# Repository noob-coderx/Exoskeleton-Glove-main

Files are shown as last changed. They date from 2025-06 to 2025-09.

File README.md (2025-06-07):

Review Assignment Due Date (https://classroom.github.com/a/NJLWAR4a)



<!-- DON'T MODIFY ANYTHING ABOVE -->

<!-- Modify from here -->
# MIRAGE - Motion Integrated Real Time Articulated Glove Emulator
This document serves as a comprehensive guide for the project submission. 
## Project Overview
The project is a portable, wearable, exoskeleton glove. The glove, once worn, is able to detect the motions of the hand and simulate the motion on Unity on our Laptop. The exoskeleton glove is 3d printed, and each finger joint has a rotary encoder in it, which is used to figure out the amount of rotation. 
### Project Name: Exoskeleton glove for sensing precise hand movements
### Team Number: Mon-16
### Team Members:
- Nishant Bhave   (22B2144)
- Prajwal Nayak   (22B4246)
- Reeyansh Shah   (22B0412)
- Shikhar Moondra (22B0688)
- Siddick Khatri  (22B4241)

### Problem Statement and Solution:
The problem statement was to build a sensing exoskeleton glove to measure precise movements of fingers. The exoskeleton glove has to sense precise angular movement of each of the joints of the finger. It needs to transmit the captured data to a laptop which will recreate this movement using a 3D hand simulation. We were expected to deliver a functional exeskeleton glove which can be worn by a user and a 3D simulated model which tracks the user's hand movements using the exoskeleton glove. Some other expectations are as follows:
- Should be able to measure 1 degree angular movements of each finger joint
- Should be able to recreate the simluated movement within 1 second lag
- Should be battery operated for atleast half hour.

We solved this problem in the following ways:
- We made a exoskeleton glove (3D printed whose files are in the 3D_models subdirectory), which has spaces to attach rotatry encoders in them and they bend enough to get a precise measurement of the bending of the joints. The rotary encoders are basically potentiometers where the angle rotated is proportional to the angle rotated given that the angle lies in the range 0 to 2 pi. 
- The readings of the encoders are read by the raspberry pi pico w (which has an inbuilt Wifi module) as values from 0 to 65536 (16 bit). These values are sent to the Printed Circuit Board (whose schematic is given in the pcb subdirectory).
- The PCB mainly has 2 multiplexers and the Raspberry pi pico W mounted on it. It has header pins for taking in the values of the encoders. The multiplexers, based on the select pin values given by the Rpi, select which rotary encoders to read. The outputs of the multiplexers are connected to the ADC pins on the Rpi. The Rpi takes these readings and sends it to the laptop wirelessly using the UDP protocol. The Rpi code was written on Thonny which I have uploaded on the /src/Rpi_code folder.
- The values sent by Rpi are recieved by a python code running on the PC which then does some slight filtering/smoothening and forwards the value to the app (designed by unity).
- The app has a rigged hand model (which was designed on blender whose design is in the others folder). It also has the code for recieving values and converting it to angles and showing the intended fingers  bending. There are two sets of calibration post which the hand starts making accurate movements (code on /src/unity_codes).

We having worked on developing an exoskeleton glove, which involved circuit design, sensor integration, and mechanical assembly.We as a team learnt a lot of technical skills from this project : 3D Modelling, Raspberry pi coding on Thonny, using multiplexers, designing PCBs, using blender, and unity (C#), wiresless transmission of data using UDP protocol This experience significantly enhanced our skills in time management, teamwork, and collaboration. We faced several challenges, particularly during PCB fabrication, which taught us the importance of early planning and maintaining buffer time to manage unforeseen delays. Working late into the night became common as we strived to meet deadlines while maintaining accuracy. We learned to divide tasks effectively, communicate clearly, and support each other through technical and logistical hurdles. A key takeaway was the ability to balance seeking guidance when necessary with independently troubleshooting problems. Overall, it was a comprehensive learning experience that combined technical rigor with essential project management and interpersonal skills.

Due to time constraints and some last minute issues of raspberry pi heating up, we were not able to power the exoskeleton glove with the battery and decided to power it using our PC instead. Nevertheless the transmission is still over wifi setup using our hotspot. We look forward to debug this issue rigorously and make the glove operational using a battery for portable deployability. The Glove has immense application in rehabilitation and VR gaming industry and although we attempt to show its functioning though the prosthetic arm, we are excited to implement this project on a standard pneumatic actuated glove to help out and do our bit for the society!

## 1. Source Code

All source code files are organized under the `/src` directory. Each subdirectory has clear descriptions about their purpose and functionality. Every subfolder has a README.MD file which explains the purpose of the code and all the commands used.

### Folder Structure:
```plaintext
/Project-Root 
├── /src 
  ├── /Rpi_code
     ├── rpi.py
  ├── /python-code
     ├── python.py
  ├── /unity_codes
     ├── /handcontroller
        ├── /Hand_control.cs
     ├── /camera_rotation
        ├── /CameraOrbit.cs
```

## 2. PCB Design

The project involves designing a printed circuit board (PCB). We have provided the design files in the `/pcb` folder. The PCB was designed using KiCAD. The picture of our final PCB Layout is present under the `/pcb/<PCB_X>/pictures` folder.

### Folder Structure:
```plaintext
/Project-Root 
├── /pcb 
  ├── /PCB1
    ├──/pictures
      ├──3D view.png
      ├──PCB layout.png
      ├──circuit.png
    ├── PCB.kicad_pcb 
    ├── pcb.kicad_sch
```
---

## 3. 3D Models
The project includes 3D models that require 3D printing. The files are placed in the `/3d_models` directory. Create separate subfolders for different models and provide a description of the design process and tools used.

### Folder Structure:
```plaintext
/Project-Root
├── /3d_models
  ├── /Exoskeleton Glove
     ├── Rot Pot V1.jpg
     ├── Rot Pot v1.stl
     ├── connect 1.jpg
     ├── connect 1.stl
     ├── connect 2.stl
     ├── connect base.jpg
     ├── connect base.stl
     ├── connect2.jpg
     ├── index sensor place 1 velcro v12.jpg
     ├── index sensor place 1 velcro v12.stl
     ├── palm base v1.jpg
     ├── palm base v1.stl
     ├── pcb case easy v1.jpg
     ├── pcb case easy v1.stl
     ├── pcb case top v1.jpg
     ├── pcb case top v1.stl
     ├── sensor body attachment back v13.jpg
     ├── sensor body attachment back v13.stl
     ├── sensor body attachment base v10.jpg
     ├── sensor body attachment base v10.stl
     ├── sensor body attachment v14.jpg
     └── sensor body attachment v14.stl
  ├── /Prosthetic Arm
     ├── Arm_Cover.jpg
     ├── Arm_Cover.stl
     ├── Assemble_Prosthetic_Arm.png
     ├── Finger_Index.jpg
     ├── Finger_Index.stl
     ├── Finger_Middle.jpg
     ├── Finger_Middle.stl
     ├── Finger_Pinky.jpg
     ├── Finger_Pinky.stl
     ├── Finger_Ring.jpg
     ├── Finger_Ring.stl
     ├── Finger_Thumb.jpg
     ├── Finger_Thumb.stl
     ├── Right_Hand.jpg
     ├── Right_Hand.stl
     ├── arm servo placement v1.jpg
     └── arm servo placement v1.stl

```
---

## 4. Bill of Materials (BOM)

A complete Bill of Materials (BOM) listing of all the hardware components used in the project is provided in this file including both parts obtained from the lab and parts ordered from external vendors or purchased locally.

### Folder Structure:
```plaintext
/Project-Root 
├── bom.xlsx
```
---

## 5. Reports and Presentations

The project presentation and reports include a brief overview of your project, objectives, design process, results, and conclusions. This should include all the milestone submission presentations.

### Folder Structure:
```plaintext
/Project-Root
  ├── /reports 
    ├── Milestone 0 P-12 MON-16.pdf
    ├── Milestone 1 P-12 MON-16.pdf
    ├── Milestone 2 P-12 MON-16.pdf
    ├── Milestone 3 P-12 MON-16.pdf
    ├── Milestone 4 P-12 MON-16.pdf
```

## 6. Other Documents
This directory consists of the Circuit digrams used, making video and the final prototype images of our poject.
### Folder Structure:
```plaintext
/Others
  ├── Circuit Diagram Prosthetic Arm.pdf.jpg
  ├── Circuit_Diagram_Exoskeleton_Glove.pdf
  ├── Making Video.mp4
  ├── Prototype Exoskeleton Glove.jpg
  ├── Prototype Prosthetic Arm.png
  └── Wiring image of Exoskeleton Glove.jpg
```

---

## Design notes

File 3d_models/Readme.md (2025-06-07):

### This directory contains the folders for the 3D Models of our Exoskeleton Glove as well as the prosthetic arm prototype
1. Exoskeleton Glove
2. Prosthetic Arm

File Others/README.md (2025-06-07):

This directory contains the final circuit diagrams of our prototype of both Exoskeleton Glove and the Prosthetic Arm, also with the images of wiring in the circuit, and the final version of our prototype. 
It also contains the User Manual which describes on how to do the Mechanical Assembly and explains the circuit connections and caliberation Modes.

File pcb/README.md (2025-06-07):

This is the folder for our PCB design. We had a single PCB.

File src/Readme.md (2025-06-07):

This is the src folder which has the codes for the raspberry pi, untiy and python code for data reception.
1. **Raspberry Pi Pico W code and ESP32 Code** in the subdirectory microcontroller.
2. **Running Unity and Running codes** in the subdirectory unity_codes.
3. **Code for using python for reception of data wirelessly** in the subdirectory python-code

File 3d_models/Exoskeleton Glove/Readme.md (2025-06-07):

### This directory contains the STL files for fabiracation (3D Printing) of the Exoskeleton Glove.
All parts have been manufactured at 50% infill density for higher strength due to delicate parts. It is advised to use normal supports with brim (outer only) so that all parts get manufactured accurately, especially the smaller complex parts

1. Connect 1, Connect 2 connect base at attached using a hinge to propogate the joint angles accurately to the rotary potentiometer.
2. Index Sensor place 1 velcro v12 features a slide locking mechanism for the rotary encoder avoiding press-fit mechanism due recurrent failure and breakage. We have assembled the sensing glove using velcro to make it compatible for any arm size.
3. sensor body attachment v14, sensor body attachment base, sensor body attachment back, and palm base constitute the components fixed on the back side of the palm. The assembly of sensor body attachment v14, sensor body attachment base, sensor body attachment back helps achieve a 2 DOF sensing of motion in the lateral and transverse plane.
4. pcb case easy v1 and pcb case top v1 are rhe enclosures for PCB with slots for wires

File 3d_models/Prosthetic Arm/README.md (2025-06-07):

### This directory contains the STL files for fabiracation (3D Printing) of the Prosthetic Arm.
[Reference](https://www.viralsciencecreativity.com/post/arduino-flex-sensor-controlled-robot-hand)

We 3D printed all the parts with 10% infill density.
All the printed parts were assembled using elastic strings and cords as shown in the final prototype.  
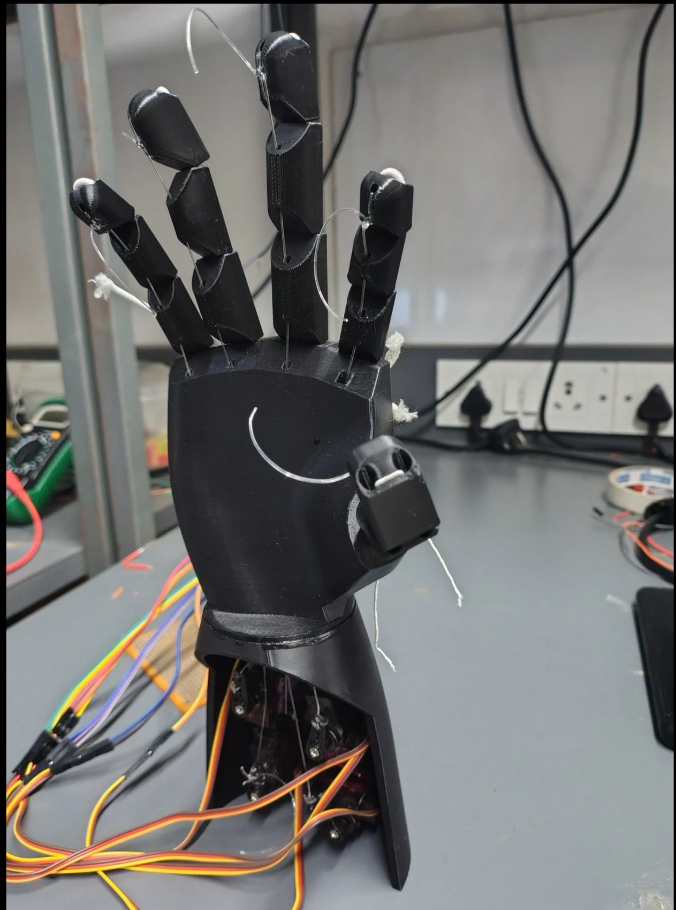
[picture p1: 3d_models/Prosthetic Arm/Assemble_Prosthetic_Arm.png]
Prosthetic Arm


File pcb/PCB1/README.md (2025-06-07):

In a nutshell, our design collects data from rotary potentiometers serially, sends them to Rpi pico which in turn quickly cycles through the available channels in a round robin fashion while powering everything using an LM2596 Buck converter

Our PCB design has the ability to support upto 24 rotary potentiometers due to which we have 24 ports connected to ground and 24 ports connected to VCC(3.3V output from sensor). We connected these to the 3.3v supply of Pico instead of our main power supply which is LM2596 because cd74hc4067 multiplexers are designed to take an input between 0 and 3.3V.
External power is inputted at the 2x1 connector which is also the input of out LM2596 buck converter, the output of this converter powers both our cd74hc multiplexers. Raspberry pico runs a program in which it outputs different values periodically at 4 different GPIO pins(2,3,4,5) which are connected to s0,s1,s2,s3 of multiplexer 1 and GPIO pins(18,19,20,21) which are connected to s0,s1,s2,s3 of multiplexer 2. The output of each of the multiplexers(sig) is connected to 2 out of 3 ADC pins in rpi pico(GPIO 26,27,28). This output is transmitted to unity and esp32 which controls the prosthetic arm

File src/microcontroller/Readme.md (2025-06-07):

# Raspberry Pi Pico W ADC MUX Communication

This project uses a **Raspberry Pi Pico W** to:
- Connect to a Wi-Fi network.
- Read analog values from two 16-channel multiplexers (MUX).
- Send these values over UDP to a laptop in real time.

The source code reads from either MUX1 or MUX2 using GPIO and ADC pins. It selects channels using S0-S3 pins and reads the analog voltage using onboard ADCs. It transmits each channel's analog reading over a UDP socket to a specified IP and port.

---

## Microcontroller Model

**Raspberry Pi Pico W**

---

## IDE Used

**Thonny IDE** (Recommended for MicroPython development)

---

## Upload and Run Instructions

### Prerequisites

1. Install **Thonny IDE** from: https://thonny.org  
2. Ensure **MicroPython firmware** is installed on your Raspberry Pi Pico W.
3. Connect your Pico W via USB.

###  Uploading the Code

1. Open Thonny.
2. Set the interpreter:  
   `Tools > Options > Interpreter > MicroPython (Raspberry Pi Pico)`
3. Paste the script into Thonny.
4. Replace:
   - `SSID` with your Wi-Fi network name.
   - `PASSWORD` with your Wi-Fi password.
   - `LAPTOP_IP` with your laptop’s IP address.
5. Click **Run (▶️)** to execute the script on the Pico W.

##  Notes

- The Pico W will print its IP address once connected to Wi-Fi.
- It loops over analog channels and transmits the value over UDP port `5005`.
- To receive data on the laptop, you can use a UDP socket script in Python or software like netcat.

---

Modifications:
- Configured GPIO and ADC pins for 2 MUX units.
- Implemented UDP communication for real-time analog data transfer.
- Optimized loop with delay for stable channel switching.

# ESP32-Based Servo Motor Control via UDP

This project enables real-time control of servo motors using joint angle data received over UDP. An ESP32 board connects to Wi-Fi and receives lower joint angles from a laptop. These angles are used to drive corresponding servo motors via a PCA9685 driver, enabling gesture replication or robotic hand motion.

## Features

- Wi-Fi-based UDP communication
- Real-time servo actuation
- Automatic joint calibration
- Rolling average filtering for noise reduction
- Smooth motor transitions to prevent jerks

## Hardware Required

- ESP32 Development Board  
- PCA9685 PWM Driver  
- Servo Motors  
- External 5V Power Supply  
- Connecting wires

## Communication Protocol

- **Format:** `<joint_number> <angle_value>` (e.g., `1 120`)  
- **Port:** 8888 (UDP)  
- **Sender:** Laptop or external device

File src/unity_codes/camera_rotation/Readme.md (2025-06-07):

This script enables the camera in a Unity scene to orbit around a target object based on mouse input. It calculates an offset and updates the camera's position and rotation every frame, providing intuitive camera control for 3D object inspection or gameplay scenes.

Upload & Run Instructions
Microcontroller Model: Not applicable – this script runs in the Unity Engine on a PC or supported platform.

IDE Used: Unity Editor (e.g., Unity 2021.3 or later)

Steps to Compile and Upload:
Open Unity Hub and create a new 3D project or open an existing one.

Add the Script:

Create a new C# script in the Assets folder named CameraOrbit.cs.

Copy and paste the script code into this file.

Assign the Script:

Attach the CameraOrbit script to your main camera in the Hierarchy.

Drag the target GameObject (the object to orbit around) into the script’s target field in the Inspector.

Run the Scene:

Click the Play button in Unity to test the camera orbit functionality.

Example Command (in Unity Console, for debug purposes):
csharp
Copy code
Debug.Log("Camera Orbit script is active");
Let me know if you want a second entry for Microcontroller2, or if you’re using this Unity camera in a larger system with real hardware!

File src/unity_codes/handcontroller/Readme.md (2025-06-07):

   - **Folder Name**: Name it according to the microcontroller, e.g., `Microcontroller1`, `Microcontroller2`.
   - **Description**: A brief description of what each microcontroller’s source code does and its role in the project in a README.md file.
   - etailed instructions on how to upload and run the code on the microcontroller. This should include:
  - The microcontroller model (e.g. STM32, RPi Pico).
  - The Integrated Development Environment (IDE) used for programming (e.g., STM32CubeIDE, VSCode, Thonny IDE).
  - Steps for compiling and uploading the code to the device.
  - Example command to upload (if applicable).
  - 3. **Code Comments**:
- Every source file should be properly commented to describe the purpose and function of each section of code.
- If you have made modifications to an existing code template or framework, comment clearly with your team name and indicate what changes were made.

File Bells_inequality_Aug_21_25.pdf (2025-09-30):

# EPR, Bell’s Inequality, and the E91 Protocol

## Gaurav S. Kasbekar Dept. of Electrical Engineering IIT Bombay

# References

## - C. Bernhardt: Chapter 5 - M. Nielsen and I. Chuang: Section 2.6

# Copenhagen Interpretation

- Named after city where Neils Bohr lived
- According to Copenhagen interpretation:
❑ Before a measurement is made, a quantum system exists in a superposition of multiple states
- e.g., particle might be considered to be in multiple locations simultaneously
❑ The act of measuring forces the system to "collapse" into a single, definite state
- Specific state it collapses into is probabilistic, i.e., it is governed by probabilities, not determined with certainty
❑ Observer or measuring apparatus plays crucial role in determining outcome of quantum event
- Observer not merely passively observing, but actively influencing system's state
- Some physicists, e.g., Einstein and Schrodinger did not subscribe to this model, in particular, to:
❑ interpretation of states jumping with given probabilities to basis states, and
❑ concept of action at a distance in entanglement
- They thought there should be a better model using:
❑ hidden variables and local realism (details later)
- John Stewart Bell devised an ingenious test, which could distinguish between above two models
- Later, several experiments based on Bell’s result were conducted, which showed that: ❑ Einstein and Schrodinger’s view was wrong and Copenhagen interpretation is correct

# Local Realism

- A concept in physics that combines two ideas: ❑locality
❑realism
- Locality:
❑an object's properties are determined only by its immediate environment
❑any influence on that object can only travel at or below speed of light ❑distant objects cannot instantaneously affect each other
- Realism:
❑objects have definite, pre-existing properties, regardless of whether they are being observed or measured
- Einstein, Boris Podolsky, and Nathan Rosen (EPR) published a paper, which stated that:
❑special theory of relativity implied that information could not travel faster than speed of light,
❑but instantaneous action at a distance (as in entangled particles) would mean that information could be sent from Alice to Bob instantaneously
- This problem known as EPR paradox

# Hidden Variables

## - Hidden variables:

### ❑properties of particles, to which we do not have access, which determine the outcomes of quantum measurements even before the measurements are actually made

## - EPR proposed that:

### ❑quantum mechanics might be incomplete because

it does not account for these hidden variables,

### ❑quantum mechanics only provides probabilistic predictions, while a more complete theory (including hidden variables) could offer deterministic outcomes

# Versions of Bell’s Inequality

## - There are several versions of Bell’s inequality - We discuss two versions

# Bell’s Inequality: Version 1 Clauser, Horne, Shimony, and Holt (CHSH Inequality)

# CHSH Inequality

- Imagine we perform following experiment, illustrated in Fig.
- Charlie prepares two particles:
❑ sends one particle to Alice, and second particle to Bob
- Once Alice receives her particle, she performs a measurement on it
- She has available two different measurement apparatuses, so she could choose to do one of two different measurements
- These measurements are of physical properties which we shall label:
❑ PQ and PR, respectively
- Alice doesn’t know in advance which measurement she will choose to perform:
❑ when she receives particle, she randomly decides which measurement to perform
- For simplicity, assume that the measurements can each have one of two outcomes, + 1 or −1
- Suppose Alice’s particle has a value:
❑ Q for the property PQ
❑ R for the property PR

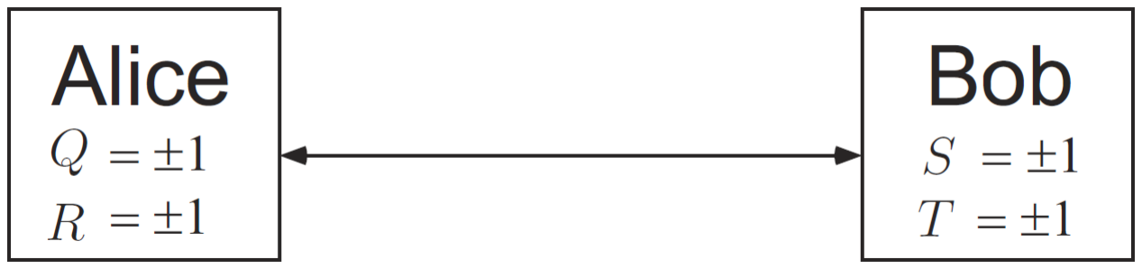
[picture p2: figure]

Ref: M. Nielsen and I. Chuang, “Quantum Computation and
Quantum Information”

# CHSH Inequality (contd.)

## - Similarly, Bob is capable of measuring one of two

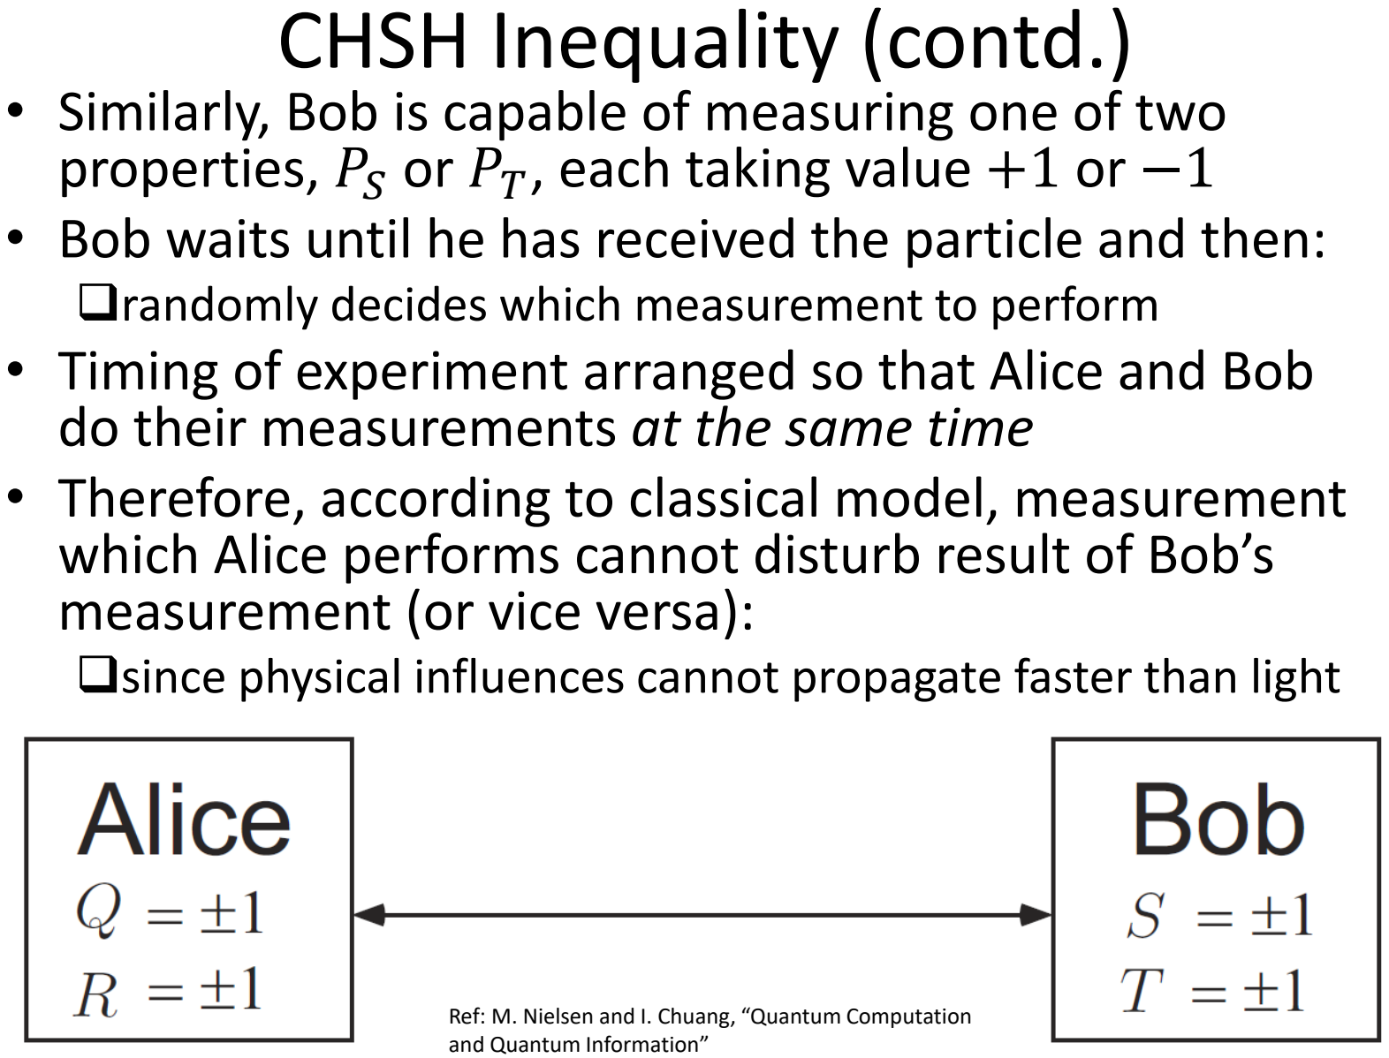
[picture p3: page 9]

## properties, PS or PT, each taking value +1 or −1 - Bob waits until he has received the particle and then:

### ❑randomly decides which measurement to perform

## - Timing of experiment arranged so that Alice and Bob do their measurements at the same time - Therefore, according to classical model, measurement which Alice performs cannot disturb result of Bob’s measurement (or vice versa):

### ❑since physical influences cannot propagate faster than light

Ref: M. Nielsen and I. Chuang, “Quantum Computation and Quantum Information”

# CHSH Inequality (contd.)

- Note that:
1) QS + RS + RT − QT = Q + R S + R − Q T
- Since R,Q ∈ {−1, +1}, it follows that:
❑ Q + R S = 0 or R − Q T = 0
- In either case, from 1), we get that:
2) QS + RS + RT − QT = ±2
- Let p(q, r, s,t) be probability that, before the measurements are performed, system is in state where Q = q, R = r, S = s, T = t
❑ these probabilities may depend on how Charlie performs his preparation, and on experimental noise
- By 2), we get:
3) E QS + E RS + E RT − E QT = σq,r,s,t p(q, r, s,t) (
)

qs + rs + rt −
qt ≤ 2
- Inequality in 3) known as CHSH inequality
- Note that we derived 3) using classical model (assumption of realism)

Ref: M. Nielsen and I. Chuang, “Quantum Computation and Quantum Information”

# CHSH Inequality (contd.)

## - Recall: CHSH inequality:

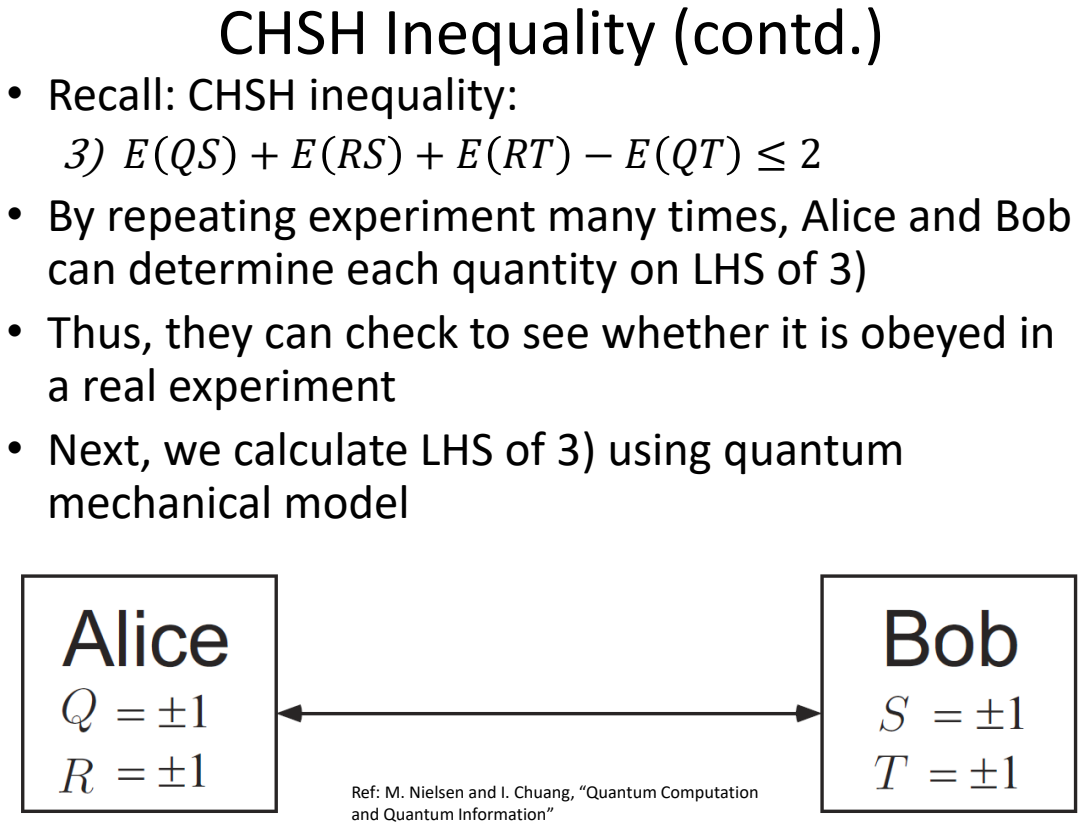
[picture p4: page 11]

• By repeating experiment many times, Alice and Bob
can determine each quantity on LHS of 3)
• Thus, they can check to see whether it is obeyed in
a real experiment
• Next, we calculate LHS of 3) using quantum
mechanical model

Ref: M. Nielsen and I. Chuang, “Quantum Computation
and Quantum Information”

# CHSH Inequality (contd.)

- Recall: CHSH inequality:
3) E QS + E RS + E RT − E QT ≤ 2
- Suppose Charlie prepares a quantum system of two qubits in state:
❑ |ψۧ =

|01ۧ−|10ۧ
2
- He passes:
❑ first qubit to Alice, and
❑ second qubit to Bob
- They perform measurements of following observables:
❑ Q = Z1, S =

−Z2−X2
2
❑ R = X1, T =

Z2−X2
2
❑ (Note: subscript 1 (respectively, 2) denotes qubit of Alice (respectively, Bob))
- Exercise: Show that eigenvalues of each of the above observables Q, R, S, and T are ±1
❑ recall: eigenvalues of observables are measurement outcomes; hence, the possible outcomes are ±1 for each observable
- Exercise: Show that average values of above observables are:
❑ QS =

1
2

; RS =

1
2

; RT =

1
2

; QT = −

1
2
❑ (use the fact that M ≡ ۦ | | ۧ(
- Thus:
4) QS + RS + RT − QT = 2 2
- Note that 3) and 4), which were obtained using classical and quantum mechanical model, respectively, contradict each other

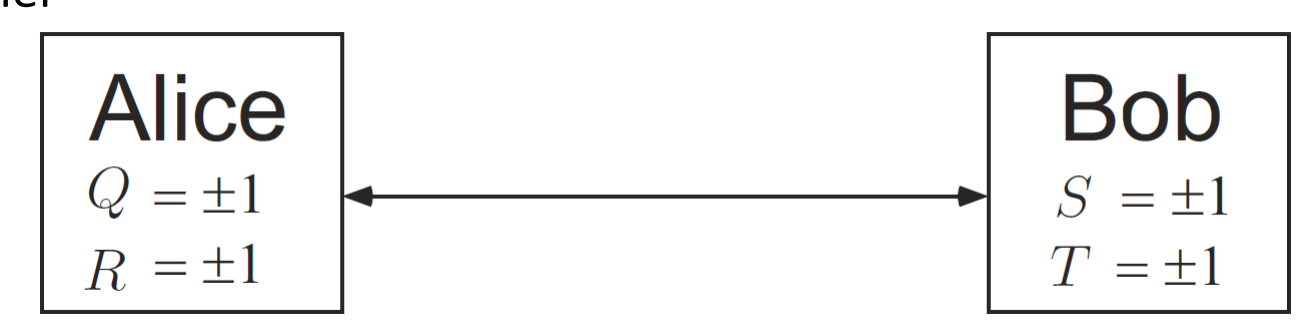
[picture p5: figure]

Ref: M. Nielsen and I. Chuang, “Quantum Computation and
Quantum Information”

# CHSH Inequality (contd.)

- Recall:
❑|ψۧ =

|01ۧ−|10ۧ
2
❑Q = Z1, S =

−Z2−X2
2
❑R = X1, T =

Z2−X2
2
- We now outline the proof of QS =

1
, which is part of above

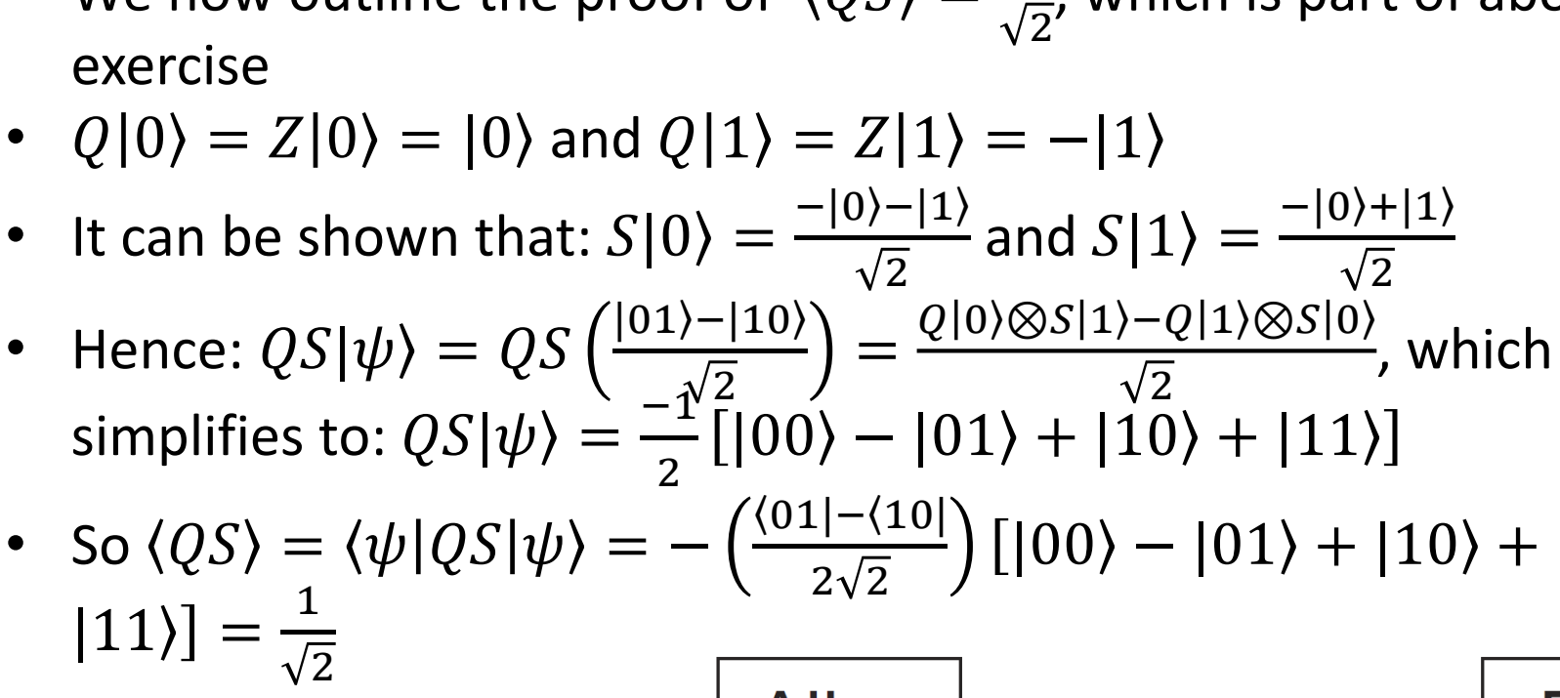
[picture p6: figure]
exercise; 0ۧ = |0ۧ and Q; • It can be shown that: S|0ۧ =; and S|1ۧ =; • Hence: QS|ψۧ = QS |01ۧ−|10ۧ; , which; simplifies to: QS|ψۧ =

Ref: M. Nielsen and I. Chuang, “Quantum Computation and
Quantum Information”

# CHSH Inequality (contd.)

- Recall:
❑ |ψۧ =

|01ۧ−|10ۧ
2
❑ Q = Z1, S =

−Z2−X2
2
❑ R = X1, T =

Z2−X2
2
- Note that we need to calculate E QS , which is the average value of the product of two scalars
- But we equated it to QS = ۦ | Q | ۧ = ۦ | ⊗ | ۧ
- Why does the tensor product Q ⊗ S correspond to the measurement outcome qs, which is a product of two scalars?
- Recall the spectral decompositions:
❑ Q = σq qPq and
❑ S = σs sPs
❑ where Pq is projector onto eigenspace of Q with eigenvalue q
- So:
❑ Q ⊗ S = σq qPq ⊗ σs sPs = σq,s qs Pq ⊗ Ps
- Hence, Q ⊗ S is an observable with corresponding measurement outcomes qs

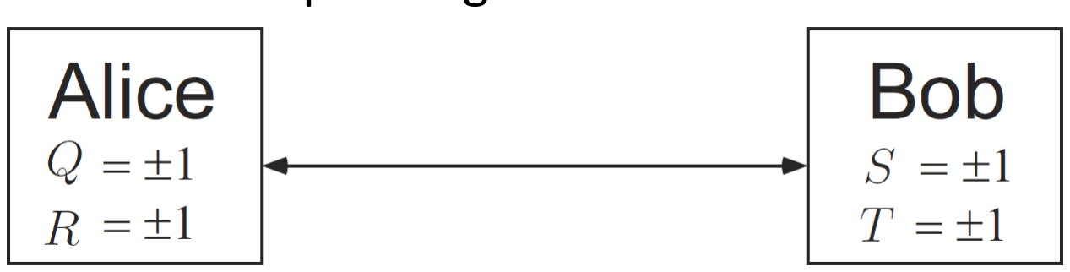
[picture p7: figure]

Ref: M. Nielsen and I. Chuang, “Quantum Computation and
Quantum Information”

# CHSH Inequality (contd.)

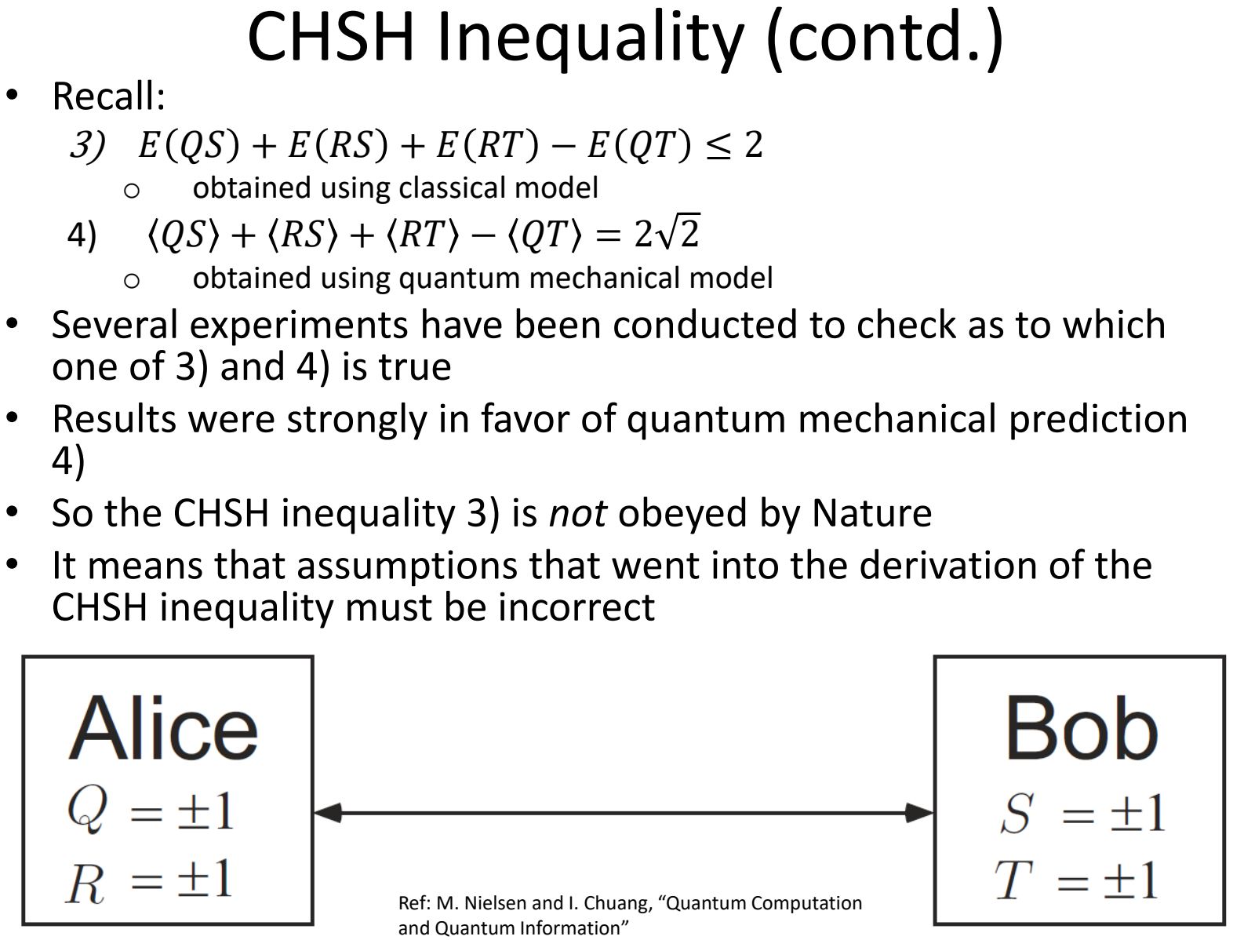
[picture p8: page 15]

- Recall:
3) E QS + E RS + E RT − E QT ≤ 2
- obtained using classical model
4) QS + RS + RT − QT = 2 2
- obtained using quantum mechanical model
- Several experiments have been conducted to check as to which one of 3) and 4) is true
- Results were strongly in favor of quantum mechanical prediction 4)
- So the CHSH inequality 3) is not obeyed by Nature
- It means that assumptions that went into the derivation of the CHSH inequality must be incorrect

Ref: M. Nielsen and I. Chuang, “Quantum Computation and Quantum Information”

# CHSH Inequality (contd.)

- Recall:
3) E QS + E RS + E RT − E QT ≤ 2
- obtained using classical model
4) QS + RS + RT − QT = 2 2
- obtained using quantum mechanical model
- There are two assumptions made in various proofs of 3) which are questionable: realism and locality ❑ Realism:
❑ assumption that the physical properties PQ, PR, PS

, and PT have definite values, Q, R, S, and T, which exist independent of observation
❑ We used this in above derivation to write E QS + E RS + E RT − E QT = σq,r,s,t p(q, r, s,t) qs + rs + rt − qt , where p(q, r, s,t) is probability that before the measurements are performed, system is in state where Q = q, R = r, S = s, T = t
❑ Note: If we try to define p(q, r, s,t) to be probability that after measurements are performed, the outcomes will be Q = q, R = r, S = s, T = t, then such a joint distribution does not exist in general since either PQ or PR (respectively, PS or PT) is measured, but not both
❑ Locality:
❑ assumption that Alice performing her measurement does not influence the result of Bob’s measurement
❑ If this assumption holds, then we can write:
❑ E QS = E Q)E(S , E RS = E R)E(S , E RT = E R)E(T , and E QT = E Q)E(T
❑ So E QS + E RS + E RT − E QT = E S E Q + E R + E T E R − E Q ≤ | E Q + E R | + | E Q − E R | ≤
2 max |E Q)|, |E(R | ≤ 2
- These two assumptions together constitute assumption of local realism:
❑ must be dropped

Ref: M. Nielsen and I. Chuang, “Quantum Computation and Quantum Information”

# Bell’s Inequality: Version 2

# Entangled Qubits in Different Bases

- Consider two entangled qubits in state:

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
- Now, consider a new orthonormal basis |b ۧ 0 , |b ۧ 1 : ❑where the components of |b ۧ 0 and |b ۧ1 are real numbers
- Claim:

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
|b ۧ 0 ⊗ |b ۧ 0 +

1
2

|b ۧ 1 ⊗ |b ۧ 1
- Proof:
❑Let |b ۧ 0 =

a
b

and |b ۧ 1 =

c
d

, where a, b, c, d ∈ R
❑Then 1
0

= a

a
b

+ c

c
d
1) So 1
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
2) Similarly, 0
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
❑Adding 1) and 2), we get: 1 0

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
= |b ۧ 0 ⊗ |b ۧ 0 + |b ۧ 1 ⊗ |b ۧ1

## Bases Used for Bell’s Inequality

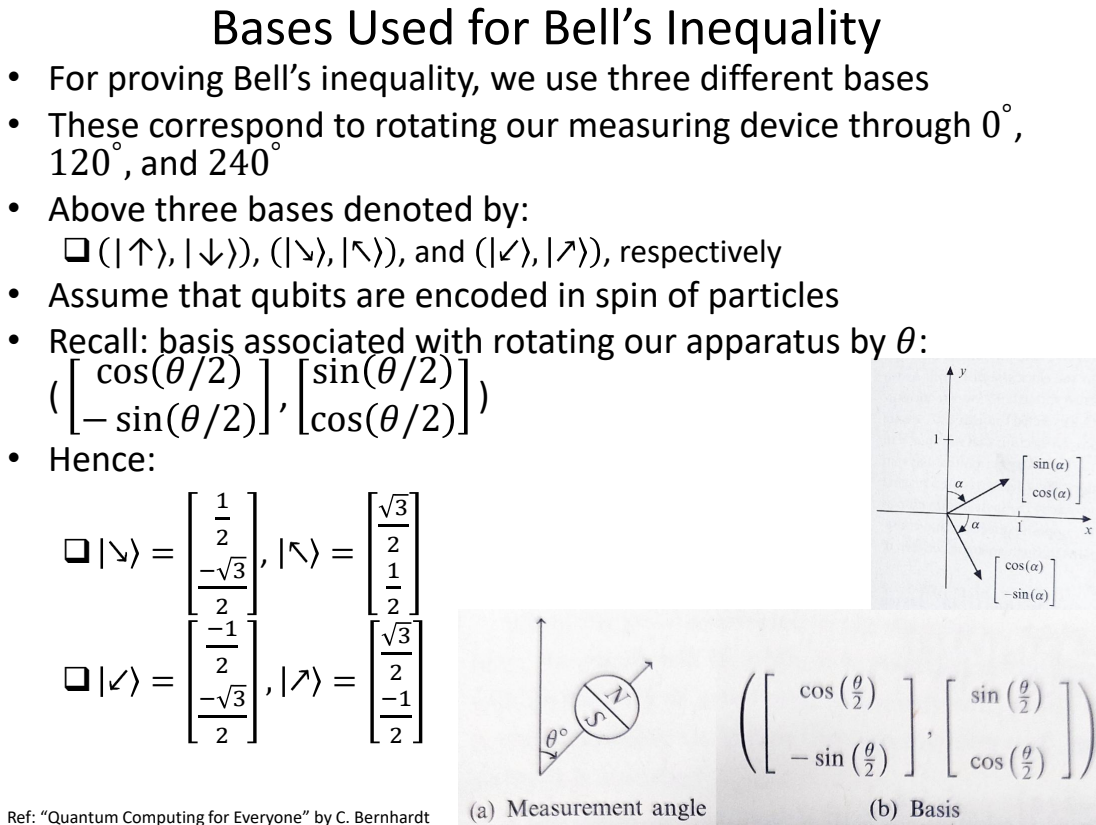
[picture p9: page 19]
, and 240; , and; , respectively; sin θ/2 cos θ/2

• For proving Bell’s inequality, we use three different bases
• These correspond to rotating our measuring device through 0
• Above three bases denoted by:
• Assume that qubits are encoded in spin of particles
• Recall: basis associated with rotating our apparatus by θ:
cos θ/2
− sin θ/2
• Hence:

Ref: “Quantum Computing for Everyone” by C. Bernhardt

# Classical Explanation of Entanglement

### - Consider two entangled qubits:

❑one with Alice and other with Bob
❑state of the qubits is 1
2

|↑ۧ|↑ۧ +

1
2

|↓ۧ|↓ۧ

### - Recall:

❑when Alice and Bob perform a measurement of their qubits in basis |↑ۧ, |↓ۧ , both get same answer (either 0 or 1)

### - Recall: for proving Bell’s inequality:

❑we rotate our measuring device through 0

°
, 120

°
, and 240

°
❑we measure spin of particles in the bases |↑ۧ, |↓ۧ , | , | ,
and | ,

### - Classical theory states:

❑there is a definite outcome of the measurement in each basis that is already determined before we perform the measurement (realism)

### - Quantum theory states:

❑outcome of measurement not determined until the time we perform the measurement

# Bell’s Inequality

- We generate a stream of n pairs of qubits:
❑ from each pair, one sent to Alice and other to Bob
- Each pair of qubits is in state:

❑

1
2

|↑ۧ|↑ۧ +

1
2

|↓ۧ|↓ۧ
- Alice:
❑ measures each qubit in direction 0

°
, 120

°
, or 240

°
- for each qubit, direction of measurement selected uniformly at random, independently of other qubits
❑ does not keep track of direction she chose for a qubit
❑ records the outcome (0 or 1) of each measurement
- Subsequently, Bob does the same for his qubits:
❑ his directions of measurements selected independently of Alice
- In this way, Alice and Bob generate strings of length n each of 0s and 1s
- What is the fraction of bits of these strings in which Alice and Bob are in agreement?
- Bell realized that quantum mechanics model and classical model gave different numbers for the answer

## Answer of Quantum Mechanics

- Consider a pair of qubits, which is in state:

❑

1
2

|↑ۧ|↑ۧ +

1
2

|↓ۧ|↓ۧ
- Recall: if Alice and Bob select same direction of measurement (i.e., same basis), their outcomes are same
- Consider case where they select different directions of measurement
- E.g.: suppose:
❑ | Alice chooses | ,
❑ | Bob chooses | ,
- Entangled state can be written as:

❑

1
2

+

1
2
- When Alice performs measurement:
❑ | she gets 0 and state jumps to | w.p.

1
2
❑ | she gets 1 and state jumps to | w.p.

1
2
- Suppose Alice gets 0 and state jumps to
- Now:
❑ | =
| 1
| 2 +
| 3
| 2
- So when Bob performs measurement:
❑ | gets 0 w.p.
| 1
| 4 and 1 w.p. | 3
| | 4
- Thus, when Alice gets 0, states of Alice and Bob agree w.p.
| | | | | 1
| | | | | 4
- Exercise: Show that even when Alice gets 1, states of Alice and Bob agree w.p.

1
4
- In summary:
❑ | when Alice chooses | , | and Bob chooses | , | , their bits agree w.p.

1
4

and disagree w.p.

3
4
- Exercise: Show that in all other cases in which Alice and Bob choose different bases, their bits agree w.p.

1
4

and disagree w.p.

3
4
- In summary, for a given pair of qubits:
❑ | w.p.
| 1
| 3

, Alice and Bob choose same basis and their bits agree w.p. 1
❑ | w.p.
| 2
| 3

, Alice and Bob choose different bases and their bits agree w.p.

| | | | | 1
| | | | | 4
- According to quantum mechanics model, what is the fraction of bits of the strings of Alice and Bob for which the bits are in agreement?
❑ | 1
| 2

- | Classical view: | Classical Answer

❑ Measurements in all directions determined right from the start
- There are eight possible configurations:
❑ 000, 001, 010, 011, 100, 101, 110, 111
❑ where the three bits in each configuration give the answer (0 or 1) if we measure a qubit in bases |↑ۧ, |↓ۧ , | , | ,
and | , | , respectively
- Due to the entanglement between qubits of Alice and Bob:
❑ for each pair of qubits, configurations of Alice and Bob are identical
- Table shows all possible outcomes of measurement, where:
❑ a, b, and c denote |↑ۧ, |↓ۧ , | , | , and | , | , respectively
❑ | x, y , where x, y ∈ {a, b, c}, denotes that Alice (respectively, Bob) measures qubit in basis x (respectively, y)
❑ Entries in table show whether measurements agree (A) or disagree (D)
- Probabilities that should be assigned to different configurations unknown
- Since Alice and Bob choose each of their three bases with equal probabilities, each of the nine pairs of bases occurs w.p.

1
9

Ref: “Quantum Computing for Everyone” by C. Bernhardt

- Note that each row contains at least five As
- Hence, overall probability that measurements of Alice and Bob result in same outcome is at least ⁵
9
- According to classical model, what is the fraction of bits of the strings of Alice and Bob for which the bits are in agreement?
❑at least ⁵
9

# Summary of Bell’s Result

## - Recall above question:

### ❑What is the fraction of bits of the strings in which Alice and Bob are in agreement?

## - Answer of quantum mechanics: ¹

2

## - Classical answer: at least ⁵

9

## - Thus, Bell’s test gives us a way to distinguish between the two theories - Above experiment has been performed by several researchers - Outcomes have always been in agreement with quantum mechanics

# E91 QKD Protocol

- In 1991, Artur Ekert proposed QKD protocol based on entangled qubits used in Bell’s test
- We generate a stream of 3n pairs of qubits:
❑ from each pair, one sent to Alice and other to Bob
- Each pair of qubits is in state:

❑

1
2

|↑ۧ|↑ۧ +

1
2

|↓ۧ|↓ۧ
- Alice and Bob measure each qubit using a random choice of three bases: ❑ as in Bell test
- As in BB84 protocol, for each measurement:
❑ Alice and Bob record both outcome and basis that they chose
- After Alice and Bob have made 3n measurements:

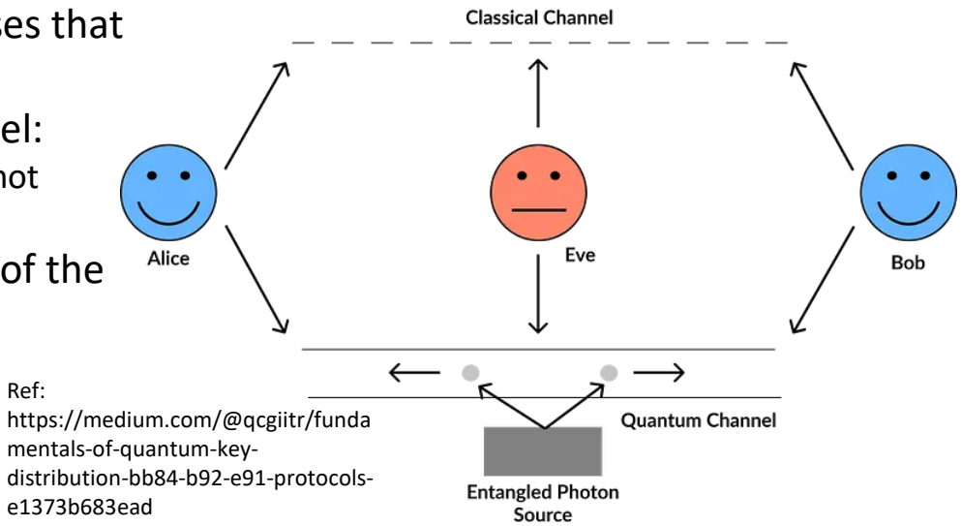
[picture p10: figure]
https://medium.com/@qcgiitr/funda mentals-of-quantum-key- distribution-bb84-b92-e91-protocols- e1373b683ead

Ref:

❑They compare the sequences of bases that
they chose
❑This can be done on insecure channel:
oNote that they only reveal bases, but not measurement outcomes
❑They will agree on approximately n of the sequence of bases

# E91 QKD Protocol (contd.)

- For the n pairs of qubits for which Alice and Bob selected same basis:
❑ Alice and Bob get same measurement outcome (0 or 1)
- This string of n bits will be their key if an eavesdropper Eve is not listening in
- Now Alice and Bob test to find if Eve is present
- If Eve is eavesdropping, she will have to measure the qubits:
❑ When she measures them, the entangled states of Alice and Bob become unentangled
- Alice and Bob look at their bits strings of length 2n each that correspond to times when they chose different bases
- From above Bell inequality calculation, they know that if their states are entangled, in each place, they should agree w.p.

1
4
- However, if Eve is measuring one of the qubits, the fraction of bits for which they agree changes
- E.g., if Eve measures a qubit before Alice and Bob have made their measurements:
❑ by checking all the possibilities, it can be shown that fraction of times that Alice and Bob will agree increases to ³
8

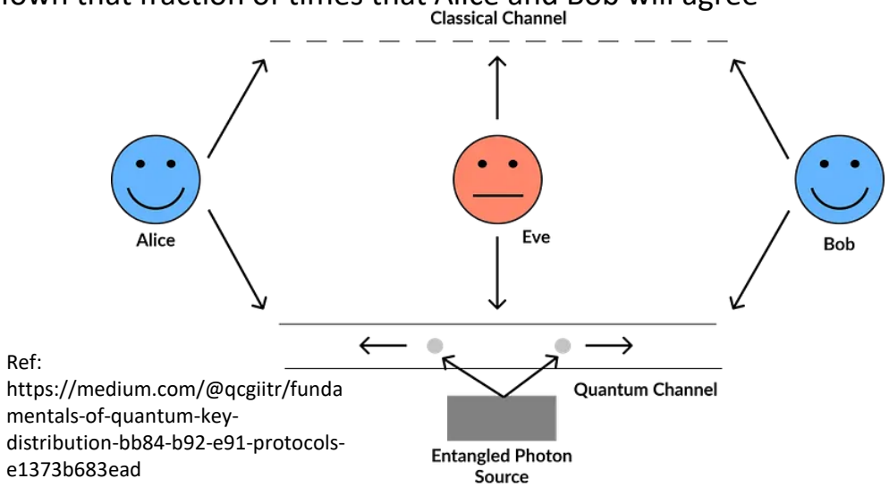
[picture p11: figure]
https://medium.com/@qcgiitr/funda mentals-of-quantum-key- distribution-bb84-b92-e91-protocols- e1373b683ead

Ref:

- Hence, Alice and Bob can use following test to check for presence of Eve:
❑They calculate fraction of the 2n qubits for which their measurement outcomes agree ❑If it is close to ¹
4

, they can conclude that
nobody has interfered and use the key

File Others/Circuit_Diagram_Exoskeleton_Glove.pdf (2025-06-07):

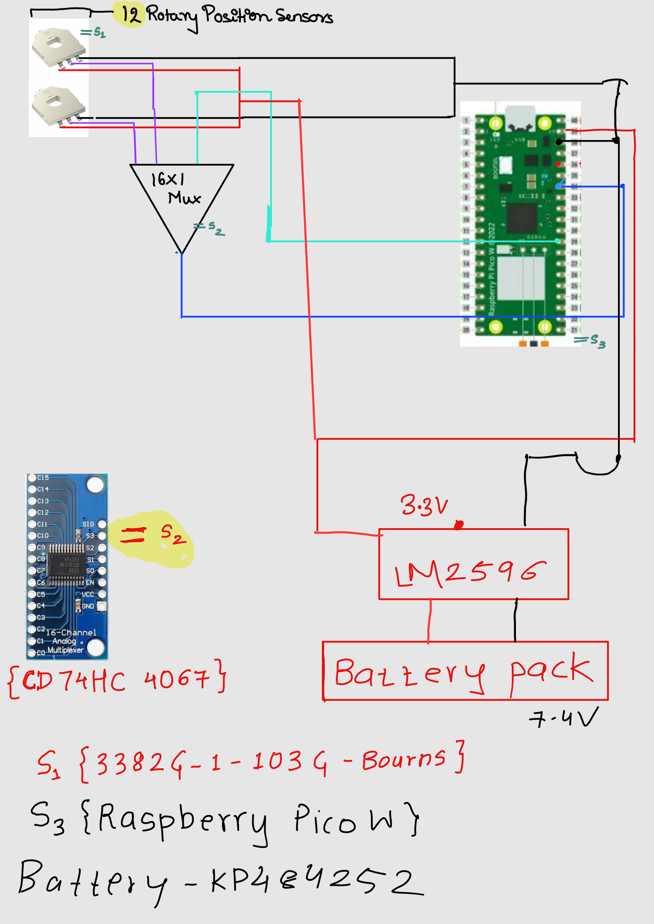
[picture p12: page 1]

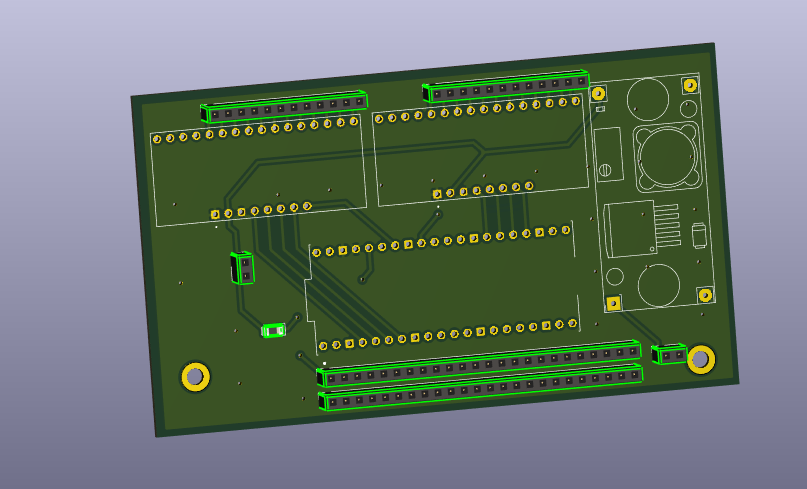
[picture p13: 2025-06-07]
pcb/PCB1/pictures/PCB layout.png

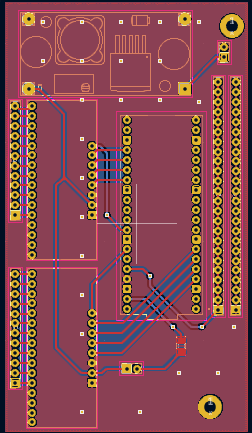
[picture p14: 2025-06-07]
pcb/PCB1/pictures/3D view.png

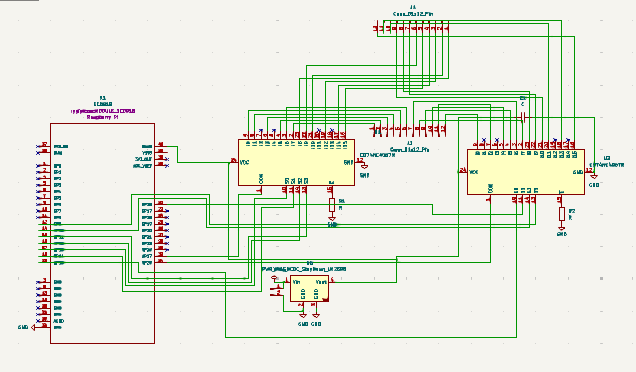
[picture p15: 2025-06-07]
pcb/PCB1/pictures/circuit.png

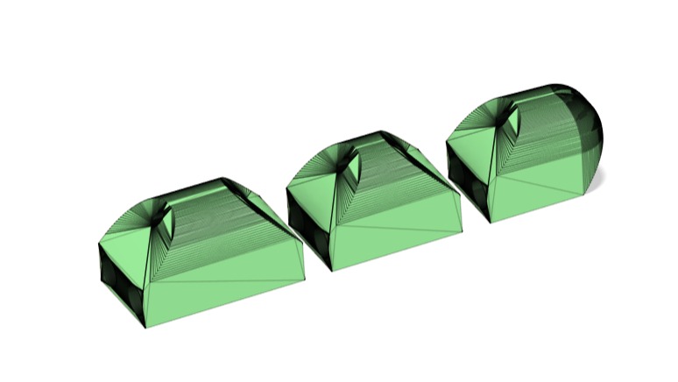
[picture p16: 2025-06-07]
3d_models/Prosthetic Arm/Finger_Pinky.jpg

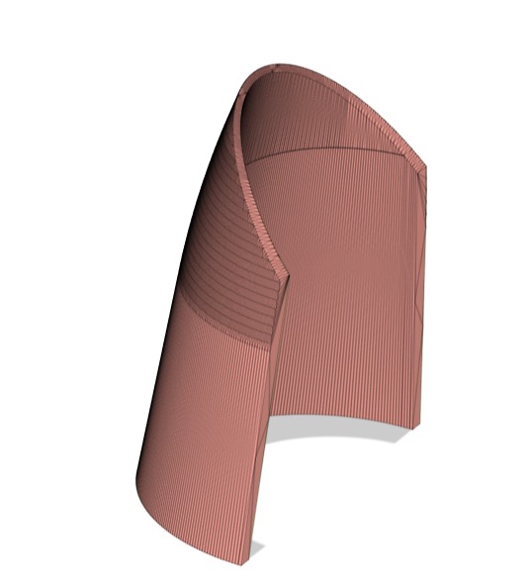
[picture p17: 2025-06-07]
3d_models/Prosthetic Arm/Arm_Cover.jpg

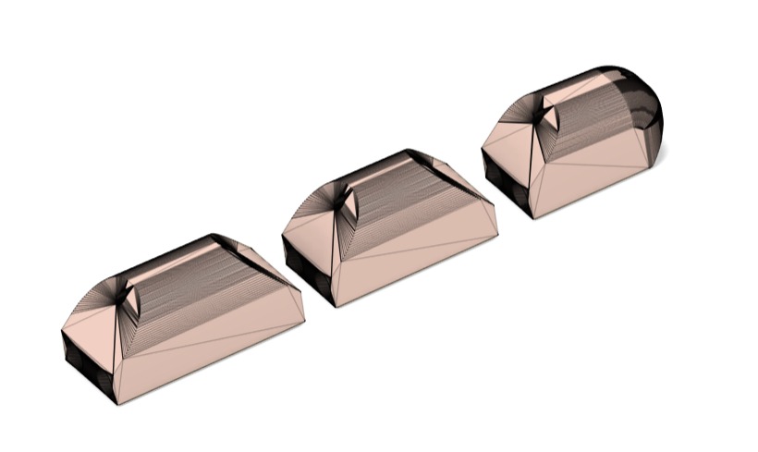
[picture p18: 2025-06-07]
3d_models/Prosthetic Arm/Finger_Ring.jpg

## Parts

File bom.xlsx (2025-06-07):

Project Title : P-12 Exoskeleton arm glove
Group ID: Monday - 16
Name of the Group Members: Shikhar Ashutosh Moondra, Prajwal Nayak, Nishant Bhave, Reeyansh shah, Siddick Khatri
Component Name | Type | Quantity | Part Number | Supplier/Manufacturer/Vendor/Purchased Place | Cost | Description
Rotary Potentiometer | Sensor | 22 | 3382g-1-103G-Bourns | Robu.in | 4290 | These sensors are being used for measuring joint angles
Raspberry Pi Pico 2 W | Microcontroller | 1 | Raspberry Pi Pico 2 W | Taken from lab | 734 | The Raspberry Pi Pico W was issued from WEL Lab
Nuts and Bolts | Utility Items | 24+4 | 2mm screws + hex 5mm bolt | Tinkerer's Laboratry | NA | The 2 mm screws were used for installing the joint measuring mechanism between connect 1 and connect 2 and connect base and 5mm bolts for PCB case cover
LM 2596 | DC-DC buck converter | 1 | LM 2596 | Robu.in | 39 | This is used to convert the 11.4V of LiPo battery down 3.3V
Jumpers and Wires | Utility Items | ~50 | NA | WEL Lab and Mangaldeep Electric & Hardware Stores | 150 | Connecting sensors to PCB and servos to servo controller
Glove | Utility Items | 1 pair | NA | Kuber Industries (From Amazon.in) | 135 | Glove for installing all the sensors
3D Printer Filament PLA | Utility Items |  |  | WEL Lab and Tech Team available printer |  | All the parts were designed by us and needed 3D printing for implementation
Analog Multiplexer | Multiplexer | 2 | CD 74hc 4067 | Robu.in | 98 | To route data from all the sensors to ADC on Raspberry Pi Pico W
Schottky Diode | Diode | 1 | MBR120 | Issued from WEL | 19 | Safety precaution to protect Raspberry Pi from power surge
Tower Pro MG90S | Servo Motor | 5 | MG90S | Mangaldeep Electric & Hardware Stores | 1000 | Actuator to operate the 5 fingers of the prosthetic arm
Elastic Cord | Utility Items | 15m | NA | Mangaldeep Electric & Hardware Stores | 125 | To pull back the fingers of the prosthetic arm in relaxed position
Elastic String | Utility Items | 5m | NA | Mangaldeep Electric & Hardware Stores | 35 | To pull down or flex the fingers of the prosthetic arm using servo motors
Servo Controller | Controller | 1 | PCA9685 | Mangaldeep Electric & Hardware Stores | 230 | To control the signals to servo while ensuring protection from power surges
ESP32 | Microcontroller | 1 | ESP32 | Mangaldeep Electric & Hardware Stores | 300 | To control the servos of the prosthetic arm using the data received from exoskeleton glove

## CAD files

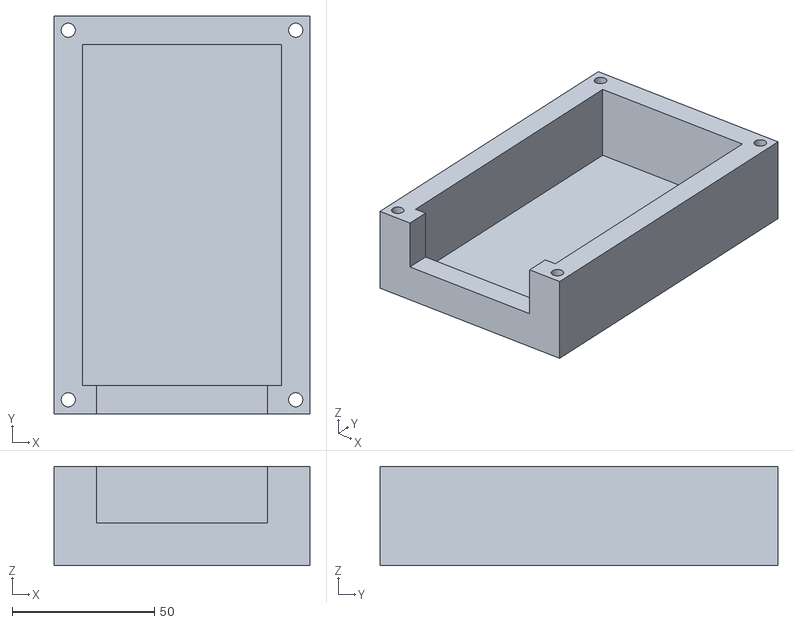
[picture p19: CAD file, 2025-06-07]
3d_models/Exoskeleton Glove/pcb case top v1.stl
90.0 x 140.0 x 35.0

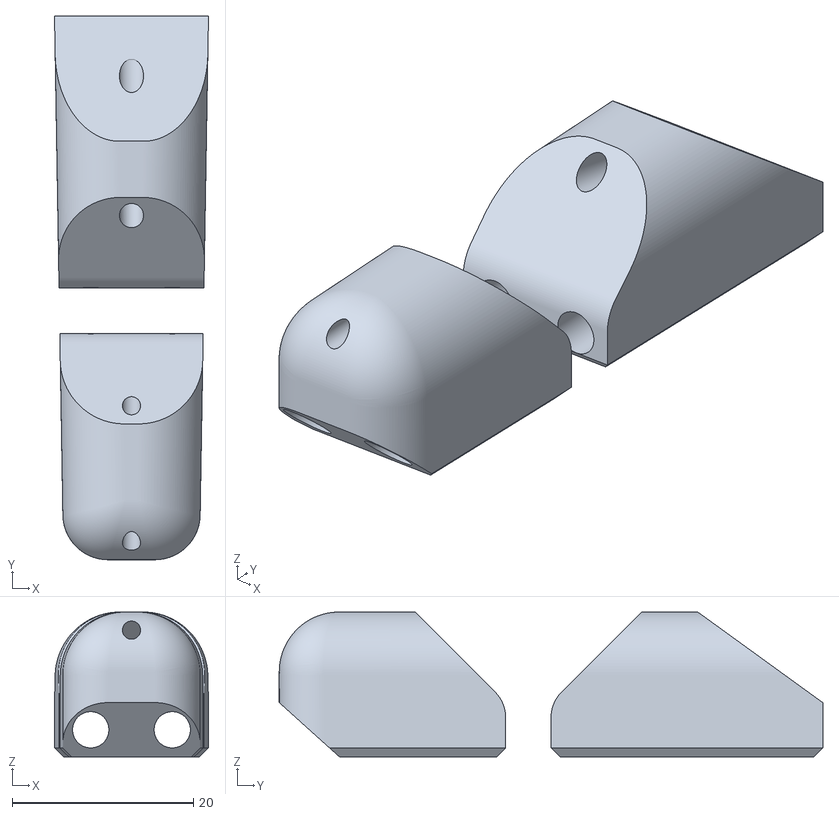
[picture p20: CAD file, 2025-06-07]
3d_models/Prosthetic Arm/Finger_Thumb.stl
17.0 x 60.0 x 16.0

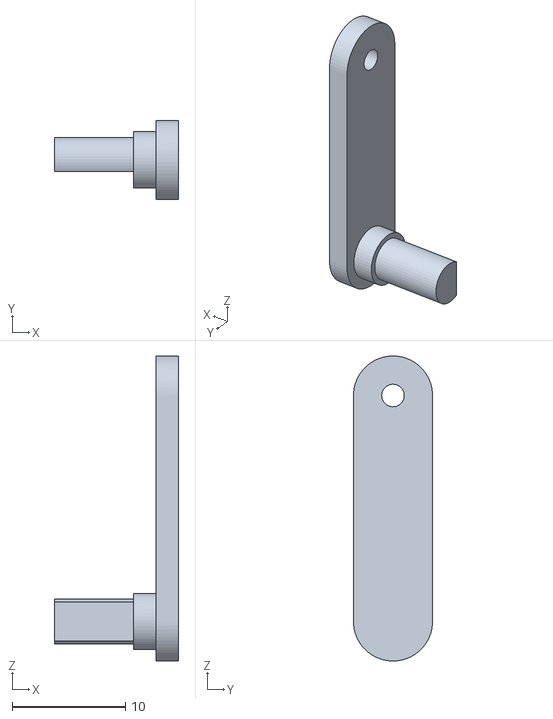
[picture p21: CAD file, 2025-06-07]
3d_models/Exoskeleton Glove/connect 2.stl
11.0 x 7.00 x 27.0

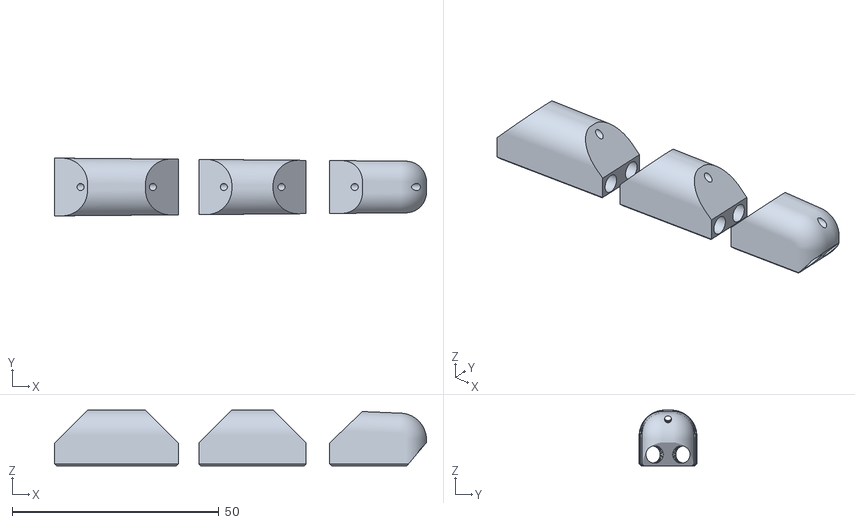
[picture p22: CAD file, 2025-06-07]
3d_models/Prosthetic Arm/Finger_Ring.stl
90.0 x 14.0 x 13.5

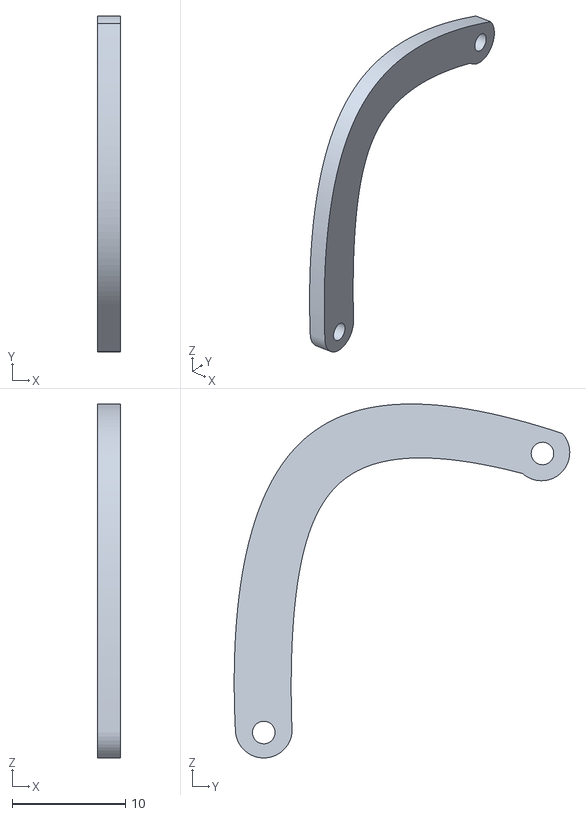
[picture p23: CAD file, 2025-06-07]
3d_models/Exoskeleton Glove/connect 1.stl
2.00 x 29.7 x 31.3

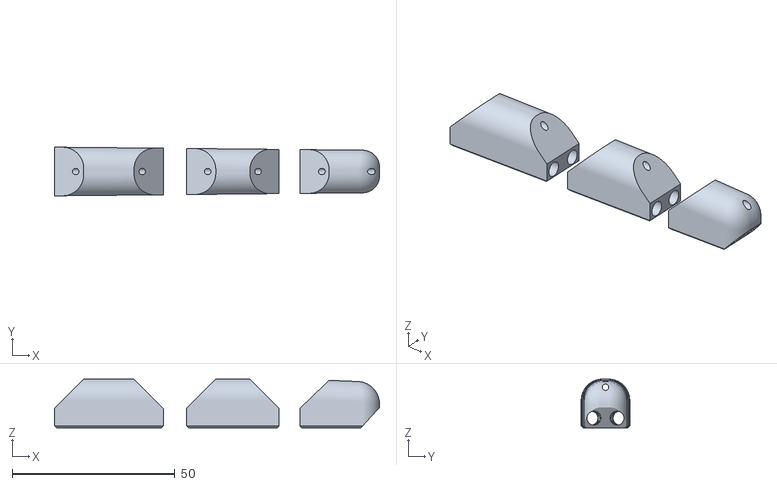
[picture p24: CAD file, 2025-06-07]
3d_models/Prosthetic Arm/Finger_Middle.stl
100.0 x 15.0 x 15.0

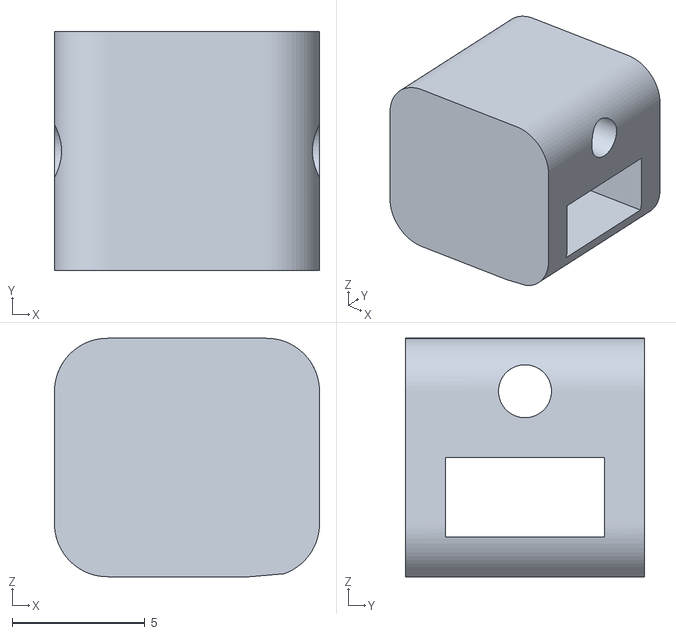
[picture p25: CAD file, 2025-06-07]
3d_models/Exoskeleton Glove/connect base.stl
10.0 x 9.00 x 9.00

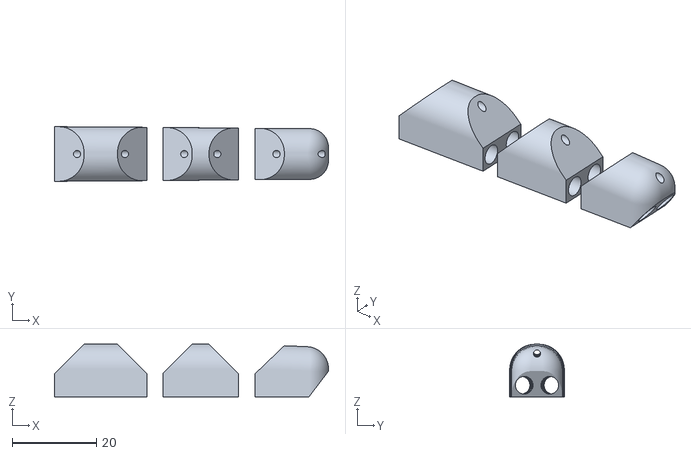
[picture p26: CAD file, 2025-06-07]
3d_models/Prosthetic Arm/Finger_Pinky.stl
65.2 x 13.0 x 12.5

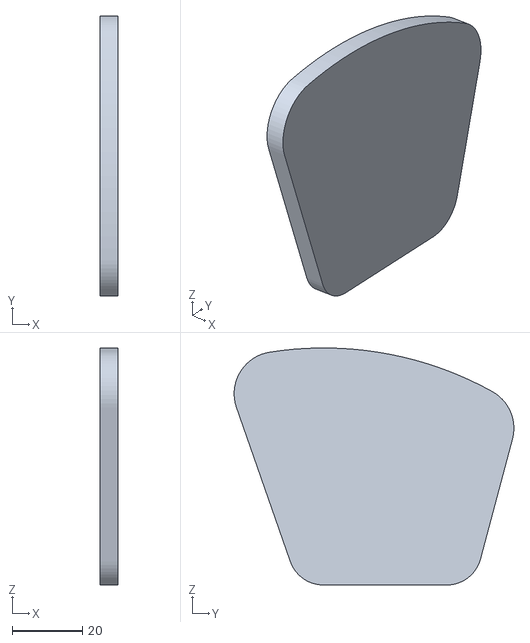
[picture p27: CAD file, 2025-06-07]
3d_models/Exoskeleton Glove/palm base v1.stl
5.00 x 79.9 x 67.7

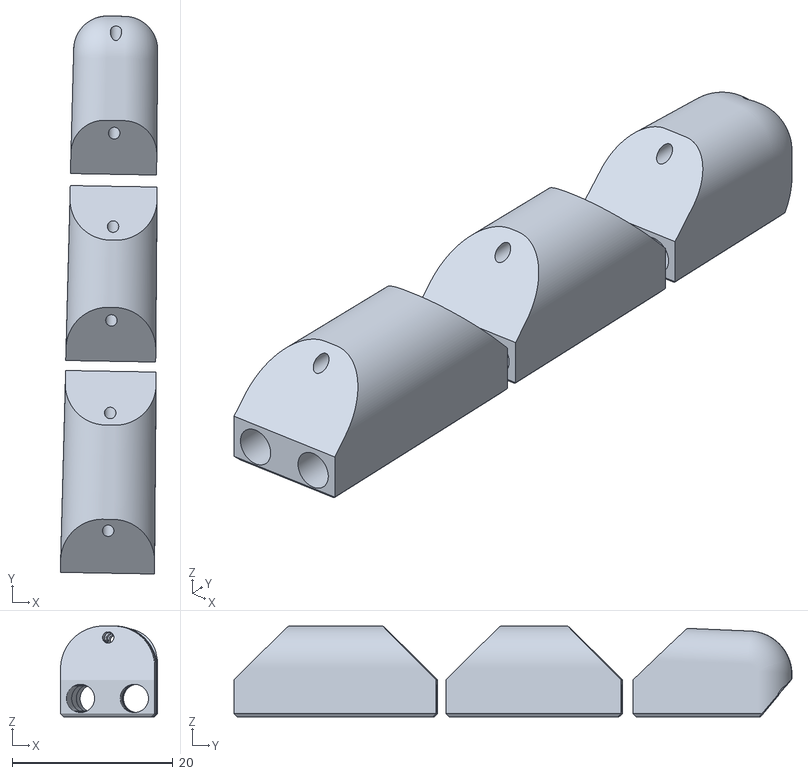
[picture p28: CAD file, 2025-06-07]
3d_models/Prosthetic Arm/Finger_Index.stl
12.1 x 69.4 x 11.3

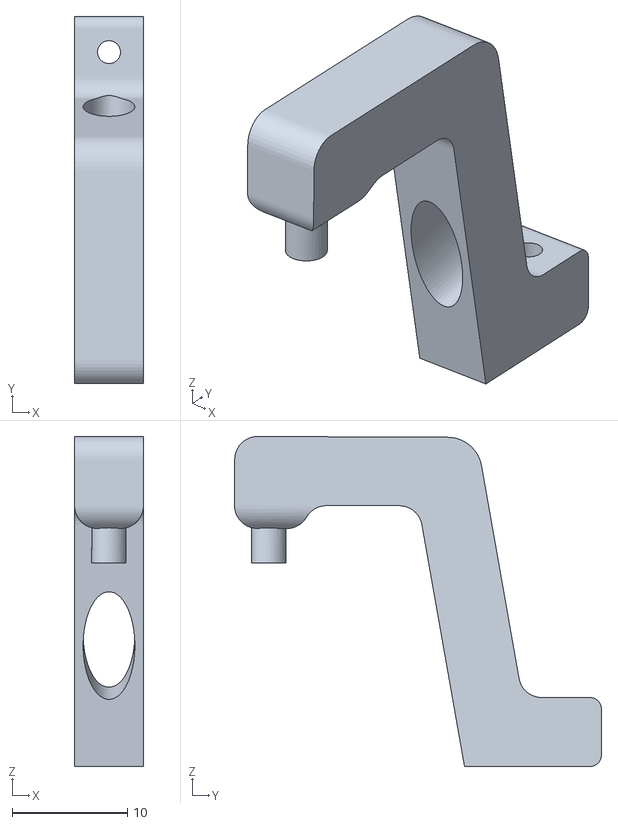
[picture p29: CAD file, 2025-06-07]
3d_models/Exoskeleton Glove/sensor body attachment back v13.stl
6.00 x 31.9 x 28.7

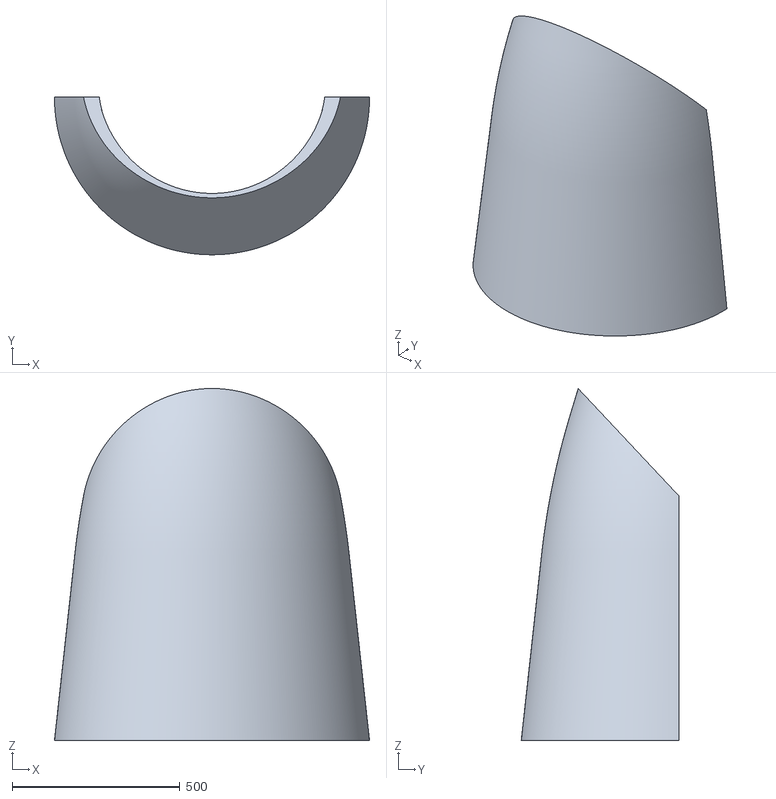
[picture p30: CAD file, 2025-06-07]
3d_models/Prosthetic Arm/Arm_Cover.stl
940.0 x 470.0 x 1050.0

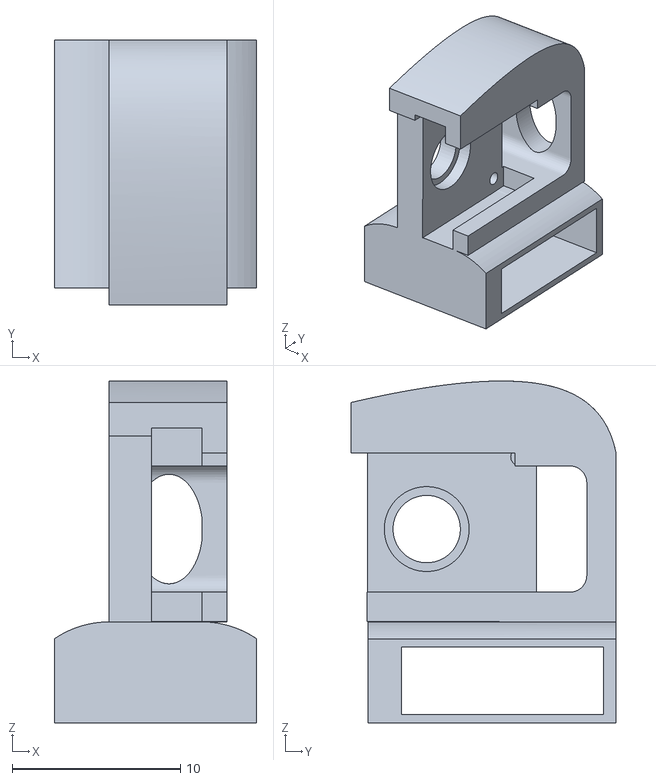
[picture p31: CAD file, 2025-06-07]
3d_models/Exoskeleton Glove/index sensor place 1 velcro v12.stl
12.0 x 15.7 x 20.3

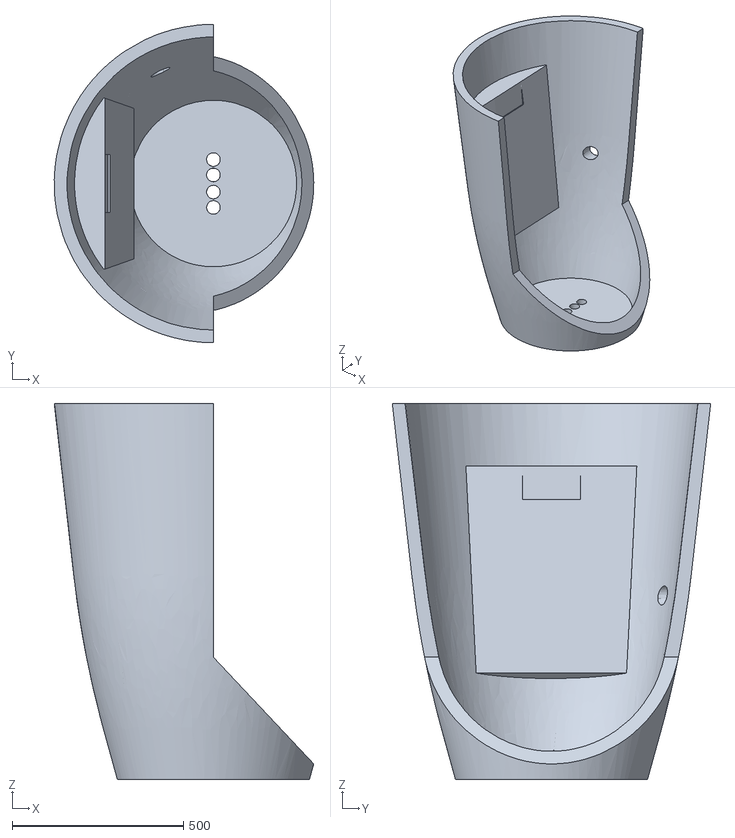
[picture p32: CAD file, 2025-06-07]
3d_models/Prosthetic Arm/arm servo placement v1.stl
758.8 x 931.0 x 1099.3

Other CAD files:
3d_models/Exoskeleton Glove/Rot Pot v1.stl
3d_models/Exoskeleton Glove/sensor body attachment base v10.stl
3d_models/Exoskeleton Glove/sensor body attachment v14.stl
3d_models/Exoskeleton Glove/pcb case easy v1.stl

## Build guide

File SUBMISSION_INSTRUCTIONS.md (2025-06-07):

# Project Documentation and Submission Guide

This document serves as a comprehensive guide for your project submission. By following the instructions below, you will ensure that the project is properly organized, documented, and easy for others (such as professors or staff members) to understand and replicate.

Your entire project is graded based on this submission and so please adhere to this properly. Stick to the hard deadline given and NO EXTENSIONS WILL BE GRANTED AT ANY POINT IF IT IS NOT COMPLETED.

## Project Overview

### Project Name: [Insert Project Name Here]
### Team Number: [MON/TUE-xx]
### Team Members:
- [Name 1]
- [Name 2]
- [Name 3]
- [Name 4]
- [Name 5] (if applicable)

### Problem Statement and Solution:

Provide a description about the project and what you've learnt and achieved in this.

Make sure to add all the below properly as given and if it's applicable.

## 1. Source Code

All source code files should be organized under the `/src` directory. If your project involves multiple microcontrollers or processors, create respective subfolders for each and provide clear descriptions about their purpose and functionality. Every subfolder should have a README.MD file which should explain the purpose of the code and all the commands used.

### Folder Structure:
```plaintext
/Project-Root 
├── /src # Source code folder (Add your source files here) 
  ├── /microcontroller1 # Code for Microcontroller 1 
    ├── file1.c # General source file 
    ├── file2.c
  ├── /microcontroller2 # Code for Microcontroller 2 (if applicable) 
    ├── file1.c # General source file 
    ├── file2.c
```

### Guidelines for Organizing Code:
1. **Microcontroller-specific code**:  
   If your project involves multiple microcontrollers, create a folder for each one under `/src`. Provide the following details:
   
   - **Folder Name**: Name it according to the microcontroller, e.g., `Microcontroller1`, `Microcontroller2`.
   - **Description**: A brief description of what each microcontroller’s source code does and its role in the project in a README.md file.

Example:
```plaintext
/src 
  ├── /<microcontroller_name1> 
    ├── <relevant_sources.c>  # All source codes
    ├── README.md  # Clear Documentation on the usage of board along with the commands and steps performed
  ├── /<microcontroller_name2> 
    ├── <relevant_sources.c>  # All source codes
    ├── README.md  # Clear Documentation on the usage of board along with the commands and steps performed
......
......
```

2. **Running the Application**:
- If your project is based on microcontroller code, provide detailed instructions on how to upload and run the code on the microcontroller. This should include:
  - The microcontroller model (e.g. STM32, RPi Pico).
  - The Integrated Development Environment (IDE) used for programming (e.g., STM32CubeIDE, VSCode, Thonny IDE).
  - Steps for compiling and uploading the code to the device.
  - Example command to upload (if applicable).

3. **Code Comments**:
- Every source file should be properly commented to describe the purpose and function of each section of code.
- If you have made modifications to an existing code template or framework, comment clearly with your team name and indicate what changes were made.

---

## 2. PCB Design (If Applicable)

If your project involves designing a printed circuit board (PCB), provide the design files in the `/pcb` folder. If you have multiple PCBs, create separate subfolders for each design. Mention the tool used to design the PCB. (KiCAD, Altium, EAGLE). Include the picture of your final PCB Layout (With visibility of all the layers) under the `/pcb/<PCB_X>/pictures` folder with the layer names along with the picture of the Printed PCB which you've obtained.

### Folder Structure:
```plaintext
/Project-Root 
├── /pcb 
  ├── /PCB1 # First PCB Design 
    ├── design.kicad_pcb # PCB Design in KiCAD format 
    ├── schematic.sch # KiCAD Schematic 
  ├── /PCB2 # Second PCB Design (if applicable) 
    ├── design.sch # PCB Schematic
    ├── design.kicad_pcb # PCB Design in KiCAD format 
```
Include all relevant design files such as schematics, board layouts, custom schematic and footprints used and imported if applicable.

---

## 3. 3D Models / Laser Cuts

If your project includes 3D models or components that require laser cutting, place these files in the `/3d_models` directory. Create separate subfolders for different models and provide a description of the design process and tools used.

### Folder Structure:
```plaintext
/Project-Root 
├── /3d_models 
  ├── /component1 # 3D Model for Component 1 
    ├── model.stl # 3D model file 
    ├── picture.png # Rendered image of the 3D model 
  ├── /component2 
    ├── model.obj 
    ├── picture.jpg
```
Make sure to also include images (e.g., PNG, JPG) of the components that were laser cut or 3D printed.

---

## 4. Bill of Materials (BOM)

Provide a complete Bill of Materials (BOM) listing all the hardware components used in your project. This should include both parts obtained from the lab and parts ordered from external vendors or purchased locally.

### Folder Structure:
```plaintext
/Project-Root 
├── bom.xls # Excel sheet listing components
```

### BOM Details:
The `bom.xls` file should include the following columns:
- **Component Name**
- **Type** (3D Model / Modules / IC / Consumables / Sensors & Actuators)
- **Quantity**
- **Part Number** (if applicable)
- **Supplier/Manufacturer/Vendor/Purchased Place**
- **Cost**
- **Description**

---

## 5. Reports and Presentations

Provide your project presentation and reports in either `.pptx`, `.ppt`, or `.pdf` format. This should include a brief overview of your project, objectives, design process, results, and conclusions. This should include all the milestone submission presentations.

### Folder Structure:
```plaintext
/Project-Root
  ├── /reports 
    ├── presentation.pptx # PowerPoint presentation file
    ├── milestone_reports.pdf # Milestone Reports in PDF file
```

## 6. Other Documents

Provide the wiring diagram of your components, attach pictures of your final project on how did you assemble the design. Place these files in the `/others` directory.
Any other important information regarding your project if it doesn't fit into any of the above categories, add it into this subfolder along with a proper README.md file to explain the same.

## Final Notes:
- **Documentation**: Ensure that all your files are well-documented. This includes commenting your code, describing your designs, and providing detailed instructions in your README file.

By following these instructions, your project will be well-organized, easy to understand, and reproducible by others, including professors or staff members who might need to verify or recreate your project in the future.

Thank you, and best of luck with your project!

---

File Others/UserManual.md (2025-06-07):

# MIRAGE  
### *Motion Integrated Real-time Articulated Glove Emulator*

---

## Mechanical Assembly

Each mechanical joint in this system corresponds to a biological joint and is named accordingly. The assembly supports **12 Degrees of Freedom (DoF)**.

### Naming Convention

Each DoF in a finger is labeled as `x.1`, `x.2`, `x.3`, where:
- `x` is the finger ID
- The digits represent the joint's position from top to bottom

#### Finger Indexing
| Finger | ID |
|---|----|
| Index Finger | 1  |
| Middle Finger  | 2  |
| Ring Finger | 3  |
| Pinky Finger | 4  *(only 2 joints)* |
| Thumb | 5  *(only 1 joint tracked)* |

#### Example
For the index finger:
- `1.1` → Top joint  
- `1.2` → Middle joint  
- `1.3` → Bottom joint

---

## Joint-to-Circuit Board Mapping

Use the following mapping for correct wiring between joints and the circuit board:

| Joint | Circuit Pin |  | Joint | Circuit Pin |
|---|---|--|---|---|
| 1.1 | C4 |  | 3.1 | C10 |
| 1.2 | C5 |  | 3.2 | C11 |
| 1.3 | C6 |  | 3.3 | C12 |
| 2.1 | C7 |  | 4.1 | C13 |
| 2.2 | C8 |  | 4.2 | C14 |
| 2.3 | C9 |  | 5.1 | C15 |

---

## Initialization Modes

### 1. **Auto-Calibration Mode**
- **Phase 1**: Keep all fingers **as straight as possible**.
- **Phase 2**: Form a **fist** (or as close to one as possible).
- The system will automatically calibrate based on these two hand postures.

### 2. **Manual-Calibration Mode**
- Involves only **one phase of calibration**.
- Uses a **default sensitivity** which can be **manually adjusted** for more accurate joint angle readings.

---

> Tip: For best results, ensure consistent posture during calibration and check sensor alignment if unexpected readings occur.

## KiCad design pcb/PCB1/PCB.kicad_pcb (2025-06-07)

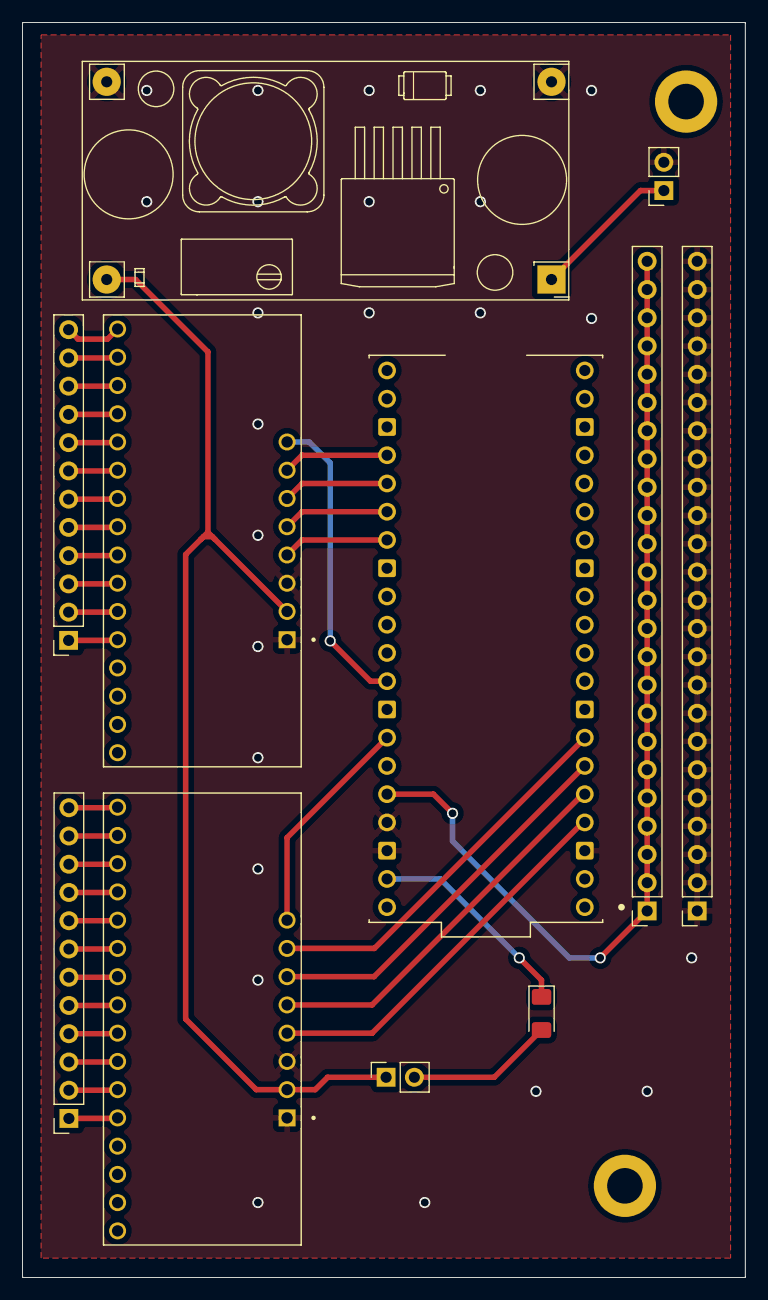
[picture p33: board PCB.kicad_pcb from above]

Board: 2 copper layers, 65.0 x 112.8 mm, 13 parts (0 on the bottom side), 40 nets.

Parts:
A1: SC0918; MODULE_SC0918
D1: D_Schottky; D_1206_3216Metric_Pad1.42x1.75mm_HandSolder
H1, H2: MountingHole_Pad; MountingHole_3.2mm_M3_DIN965_Pad
J1, J2: Conn_01x12_Pin; PinSocket_1x12_P2.54mm_Vertical
J3, J6: Conn_01x02_Pin; PinSocket_1x02_P2.54mm_Vertical
J4, J5: Conn_01x24_Socket; PinSocket_1x24_P2.54mm_Vertical
U1, U2: BOB-09056; MODULE_BOB-09056
U6: YAAJ_DCDC_StepDown_LM2596

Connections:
/Out_1: A1.34 (GP28), U1.JP3-8 (COM)
/Out_2: A1.32 (GP27), U2.JP3-8 (COM)
/S0: A1.24 (GP18), U2.JP3-7 (S3)
/S0_2: A1.7 (GP5), U1.JP3-7 (S3)
/S1: A1.25 (GP19), U2.JP3-6 (S2)
/S1_2: A1.6 (GP4), U1.JP3-6 (S2)
/S2: A1.26 (GP20), U2.JP3-5 (S1)
/S2_2: A1.5 (GP3), U1.JP3-5 (S1)
/S3: A1.27 (GP21), U2.JP3-4 (S0)
/S3_2: A1.4 (GP2), U1.JP3-4 (S0)
GND: A1.3 (GND), A1.37 (3V3_EN), A1.38 (GND), J3.2, J4.1, J4.2, J4.3, J4.4, J4.5, J4.6, J4.7, J4.8, J4.9, J4.10, J4.11, J4.12, J4.13, J4.14, J4.15, J4.16, J4.17, J4.18, J4.19, J4.20, J4.21, J4.22, J4.23, J4.24, U1.JP3-1 (GND), U1.JP3-3 (EN), U2.JP3-1 (GND), U2.JP3-3 (EN), U6.2 (GND), U6.3 (GND)
unnamed: A1.36 (3V3_OUT), J5.1, J5.2, J5.3, J5.4, J5.5, J5.6, J5.7, J5.8, J5.9, J5.10, J5.11, J5.12, J5.13, J5.14, J5.15, J5.16, J5.17, J5.18, J5.19, J5.20, J5.21, J5.22, J5.23, J5.24
unnamed: A1.39 (VSYS), D1.1 (K)
unnamed: D1.2 (A), J6.2
unnamed: J1.1, U1.JP1-5 (C4)
unnamed: J1.2, U1.JP1-6 (C5)
unnamed: J1.3, U1.JP1-7 (C6)
unnamed: J1.4, U1.JP1-8 (C7)
unnamed: J1.5, U1.JP1-9 (C8)
unnamed: J1.6, U1.JP1-10 (C9)
unnamed: J1.7, U1.JP1-11 (C10)
unnamed: J1.8, U1.JP1-12 (C11)
unnamed: J1.9, U1.JP1-13 (C12)
unnamed: J1.10, U1.JP1-14 (C13)
unnamed: J1.11, U1.JP1-15 (C14)
unnamed: J1.12, U1.JP1-16 (C15)
unnamed: J2.1, U2.JP1-5 (C4)
unnamed: J2.2, U2.JP1-6 (C5)
unnamed: J2.3, U2.JP1-7 (C6)
unnamed: J2.4, U2.JP1-8 (C7)
unnamed: J2.5, U2.JP1-9 (C8)
unnamed: J2.6, U2.JP1-10 (C9)
unnamed: J2.7, U2.JP1-11 (C10)
unnamed: J2.8, U2.JP1-12 (C11)
unnamed: J2.9, U2.JP1-13 (C12)
unnamed: J2.10, U2.JP1-14 (C13)
unnamed: J2.11, U2.JP1-15 (C14)
unnamed: J2.12, U2.JP1-16 (C15)
unnamed: J3.1, U6.1 (Vin)
unnamed: J6.1, U1.JP3-2 (VCC), U2.JP3-2 (VCC), U6.4 (Vout)

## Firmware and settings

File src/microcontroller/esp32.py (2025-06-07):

import socket
import network
from machine import I2C, Pin
from time import sleep_ms
from pca9685 import PCA9685

# ============================
# WiFi Setup
# ============================

# Connect to a WiFi network using SSID and password
ssid = 'Prajwal'
password = 'nicemice'
sta_if = network.WLAN(network.STA_IF)
sta_if.active(True)

# Wait until connected
if not sta_if.isconnected():
    sta_if.connect(ssid, password)
    while not sta_if.isconnected():
        pass

print('Connected, IP:', sta_if.ifconfig()[0])

# ============================
# I2C and PCA9685 Setup
# ============================

# Initialize I2C on pins 21 (SDA) and 22 (SCL)
i2c = I2C(0, scl=Pin(22), sda=Pin(21))

# Initialize PCA9685 PWM controller
pca = PCA9685(i2c)
pca.freq(50)  # Set frequency for servo motors (usually 50Hz)

# ============================
# Servo Control Function
# ============================

# Convert angle to PWM duty and set servo position
def set_servo_angle(channel, angle):
    min_pulse = 1000  # microseconds
    max_pulse = 2000
    pulse = int(min_pulse + (max_pulse - min_pulse) * angle / 180)
    duty = int(pulse * 4096 / 20000)  # Convert pulse width to duty cycle
    pca.duty(channel, duty)

# Smoothly move servo from current to target angle in steps
def smooth_step(channel, current, target, step):
    while current != target:
        if current < target:
            current += step
            current = min(current, target)
        elif current > target:
            current -= step
            current = max(current, target)
        set_servo_angle(channel, current)
        sleep_ms(20)  # Small delay between steps
    return current

# ============================
# Rolling Average Function
# ============================

# Maintain a rolling average over a fixed number of values
def update_rolling_average(buffer, new_val, size=10):
    buffer.append(new_val)
    if len(buffer) > size:
        buffer.pop(0)
    return sum(buffer) / len(buffer)

# ============================
# Joint Configuration
# ============================

# Define joint configurations with control channels, angles, and movement parameters
joints = {
    11: {'name': 'thumb',  'channel': 0, 'threshold': 45, 'min': -40,   'max': 60,  'step': 10},
    1:  {'name': 'index',  'channel': 2, 'threshold': 45, 'min': 25,    'max': -120, 'step': -14},
    4:  {'name': 'middle', 'channel': 4, 'threshold': 45, 'min': 300,   'max': 120, 'step': -18},
    7:  {'name': 'ring',   'channel': 6, 'threshold': 45, 'min': 130,   'max': 300, 'step': 17},
    10: {'name': 'pinky',  'channel': 8, 'threshold': 45, 'min': 220,   'max': -100, 'step': -32}
}

# ============================
# State Tracking for Each Joint
# ============================

# Maintain calibration data, recent values, and current position for each joint
joint_data = {
    j: {
        'init_vals': [],          # First 10 values for calibration
        'initial_avg': None,      # Average value used as baseline
        'recent_vals': [],        # Last N values for rolling average
        'moving_avg': None,       # Current rolling average
        'current_angle': joints[j]['min']  # Start at min position
    } for j in joints
}

# ============================
# Startup Movement Demo
# ============================

print("Running startup finger test...")
for j in joints:
    channel = joints[j]['channel']
    min_angle = joints[j]['min']
    max_angle = joints[j]['max']
    step = joints[j]['step']
    
    # Move finger to max and back to min position
    print(f"{joints[j]['name']} going to MAX...")
    smooth_step(channel, min_angle, max_angle, step)
    sleep_ms(500)
    
    print(f"{joints[j]['name']} returning to MIN...")
    smooth_step(channel, max_angle, min_angle, step)
    
    joint_data[j]['current_angle'] = min_angle
    sleep_ms(200)

print("Demo complete. Starting calibration and control...")

# ============================
# UDP Server Setup
# ============================

# Listen for UDP messages on port 8888
udp = socket.socket(socket.AF_INET, socket.SOCK_DGRAM)
udp.bind(('0.0.0.0', 8888))
print("UDP Server listening on port 8888...")

# ============================
# Main Loop: Calibration + Control
# ============================

while True:
    data, addr = udp.recvfrom(1024)  # Receive UDP packet
    msg = data.decode().strip()
    print(f"Received: {msg}")

    try:
        # Parse the incoming message
        joint_str, angle_str = msg.split(" ")
        joint = int(joint_str)
        received_angle = int(angle_str)

        # Process only if it's a valid joint
        if joint in joints:
            jd = joint_data[joint]     # Joint-specific data
            ji = joints[joint]         # Joint config

            # Extract relevant joint properties
            channel = ji['channel']
            threshold = ji['threshold']
            name = ji['name']
            min_angle = ji['min']
            max_angle = ji['max']
            step = ji['step']

            # === Calibration Phase ===
            if jd['initial_avg'] is None:
                jd['init_vals'].append(received_angle)
                print(f"[{name}] Calibrating: {len(jd['init_vals'])}/10")
                
                # Once 10 values are received, set calibration average
                if len(jd['init_vals']) == 10:
                    jd['initial_avg'] = sum(jd['init_vals']) / 10
                    print(f"[{name}] Calibration done. Initial Avg: {jd['initial_avg']:.2f}")
                    
                    # Return joint to starting position
                    jd['current_angle'] = smooth_step(channel, jd['current_angle'], min_angle, step)
            else:
                # === Post-Calibration: Rolling Average Movement Control ===
                moving_avg = update_rolling_average(jd['recent_vals'], received_angle, size=10)
                jd['moving_avg'] = moving_avg

                # Calculate deviation from baseline
                diff = moving_avg - jd['initial_avg']
                print(f"[{name}] Δ = {diff:.2f} (MovingAvg: {moving_avg:.2f}, CalibAvg: {jd['initial_avg']:.2f})")

                # If change exceeds threshold, move the joint
                if abs(diff) > threshold:
                    target = max_angle if diff > 0 else min_angle
                    if jd['current_angle'] != target:
                        jd['current_angle'] = smooth_step(channel, jd['current_angle'], target, step)
                        print(f"[{name}] Moving to {jd['current_angle']}")
                    else:
                        print(f"[{name}] Already at target.")
                else:
                    print(f"[{name}] Within threshold. No move.")
        else:
            print("Unknown joint number.")

    except Exception as e:
        print("Invalid message format or error:", e)

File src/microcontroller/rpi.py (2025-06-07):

import network  # This is the library for network connections
import socket   # This is the library for UDP communication
import time    # This is the library for time-related functions
from machine import Pin, ADC    # This is the library for GPIO and ADC functions
SSID = "SSID" # Replace with your Wi-Fi SSID
PASSWORD ="password"    # Replace with your Wi-Fi password
wlan = network.WLAN(network.STA_IF)   # Create a WLAN object for station mode
wlan.active(True)    # Activate the WLAN interface
wlan.connect(SSID, PASSWORD)   # Connect to the Wi-Fi network
while not wlan.isconnected():    # Wait for the connection to be established
    print("Connecting to Wi-Fi...")    # Print a message while connecting
    time.sleep(1)    # Sleep for 1 second to avoid busy waiting
print("Connected! Pico W IP:", wlan.ifconfig()[0])   # Print the IP address of the Pico W
# Set up UDP communication
LAPTOP_IP = "192.168.239.106" # Replace with your laptop's IP address   
UDP_PORT = 5005  # Port for Raspberry Pi to send data
# Create a UDP socket for sending data to the laptop
sock = socket.socket(socket.AF_INET, socket.SOCK_DGRAM)    # Create a UDP socket for sending data to the laptop
m2_s0 = Pin(2, Pin.OUT) # Pin for MUX 2 S0
m2_s1 = Pin(3, Pin.OUT) # Pin for MUX 2 S1
m2_s2 = Pin(4, Pin.OUT) # Pin for MUX 2 S2
m2_s3 = Pin(5, Pin.OUT)     # Pin for MUX 2 S3
m1_s3 = Pin(18, Pin.OUT) # Pin for MUX 1 S3
m1_s2 = Pin(19, Pin.OUT)    # Pin for MUX 1 S2
m1_s1 = Pin(20, Pin.OUT)    # Pin for MUX 1 S1
m1_s0 = Pin(21, Pin.OUT)        # Pin for MUX 1 S0
mux1 = ADC(Pin(27)) # ADC for MUX 1
mux2 = ADC(Pin(28)) # ADC for MUX 2
number2 = 4 # Start with the first channel of MUX 1
# Function to set the MUX channel
try:              # Infinite loop to keep the program running
    while True:  # Loop to continuously read data from the MUX and send it to the laptop
        if number2 <= 16 :  # Check if the channel number is less than or equal to 16
            number = number2    # Calculating binary of number2
            s3 = number//8     # Calculate the value for S3
            number = number % 8   # Update the number for the next calculation
            s2 = number//4     # Calculate the value for S2
            number = number % 4     # Update the number for the next calculation
            s1 = number//2   # Calculate the value for S1
            s0 = number%2  # Calculate the value for S0
            m1_s0.value(s0) # Set the value for S0 of MUX 1
            m1_s1.value(s1) # Set the value for S1 of MUX 1
            m1_s2.value(s2) # Set the value for S2 of MUX 1 
            m1_s3.value(s3) # Set the value for S3 of MUX 1
            time.sleep(0.01) # Sleep for 10 milliseconds to allow the MUX to switch channels
            analog_value = mux1.read_u16() # Read the analog value from MUX 1
            message = f"{number2 - 4} " +f"{analog_value}" # Create the message to send to the laptop
            sock.sendto(message.encode(), (LAPTOP_IP, UDP_PORT)) # Send the message to the laptop
            print(f"Sent: {message}") # Print the sent message for debugging
        else : # If the channel number is greater than 16, switch to MUX 2
            number = number2 - 12 # Calculate the channel number for MUX 2
            s3 = number//8   # Calculate the value for S3
            number = number % 8  # Update the number for the next calculation
            s2 = number//4 # Calculate the value for S2
            number = number % 4     # Update the number for the next calculation
            s1 = number//2 # Calculate the value for S1
            s0 = number%2 # Calculate the value for S0
            m2_s0.value(s0) # Set the value for S0 of MUX 2
            m2_s1.value(s1)     # Set the value for S1 of MUX 2
            m2_s2.value(s2)     # Set the value for S2 of MUX 2
            m2_s3.value(s3 )     # Set the value for S3 of MUX 2
            time.sleep(0.01) # Sleep for 10 milliseconds to allow the MUX to switch channels
            analog_value = mux2.read_u16() # Read the analog value from MUX 2
            message = f"{number2 - 4} " +f"{analog_value}" # Create the message to send to the laptop
            sock.sendto(message.encode(), (LAPTOP_IP, UDP_PORT)) # Send the message to the laptop
            print(f"Sent: {message}") # Print the sent message for debugging
        if(number2 == 15): # If the channel number is 15, switch to MUX 2
          number2 = 4 # Reset the channel number to 4
        else: # If the channel number is not 15, increment it by 1
          number2 = number2 + 1 # Increment the channel number by 1
except KeyboardInterrupt:    # Handle keyboard interrupt (Ctrl+C) to stop the program gracefully
    print("Stopping...") # Print a message indicating that the program is stopping
